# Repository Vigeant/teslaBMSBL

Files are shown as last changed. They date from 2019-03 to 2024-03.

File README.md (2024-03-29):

# teslaBMSBL

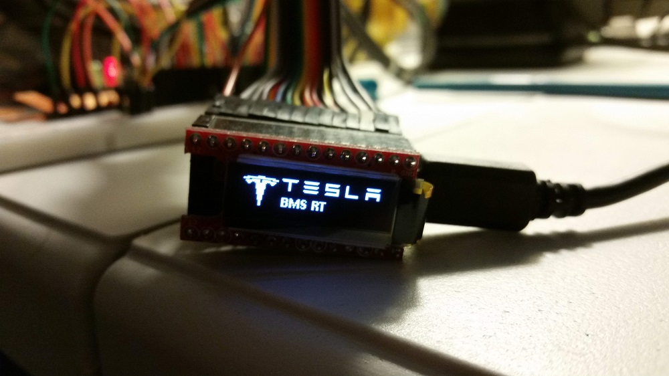
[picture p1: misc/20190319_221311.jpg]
Tesla BMS BL

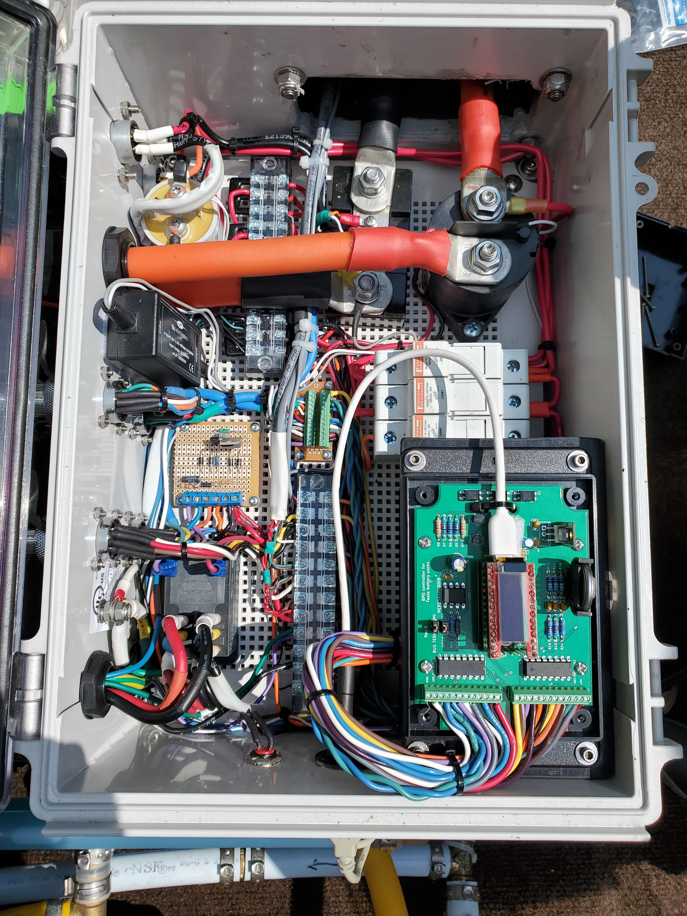
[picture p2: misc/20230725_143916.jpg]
Tesla BMS BL board


## Hardware

see eagle files to build the board hosting the teensy 3.2.

## dependencies

- TeensyView libs
  - <https://github.com/sparkfun/SparkFun_TeensyView_Arduino_Library/tree/master/examples>
- Snooze for lower power consumption
  - <https://github.com/duff2013/Snooze>

## Error codes on teensyView

| code | definition |
|:----:|---|
| A | Modules Fault Loop |
| B | Battery Monitor Fault |
| C | BMS Serial communication Fault |
| D | BMS Cell Over Voltage Fault |
| E | BMS Cell Under Voltage Fault |
| F | BMS Over Temperature Fault |
| G | BMS Under Temperature Fault |
| H | BMS 12V Battery Over Voltage Fault |
| I | BMS 12V Battery Under Voltage Fault |
| J | BMS Water Sensor 1 Fault |
| K | BMS Water Sensor 2 Fault |
| L | Incorrect modules count |

## Connection to USB serial console

Serial Line: COMX (X typically = 7)
Speed: 115200

## controller state machine

<!-- [State machine](https://online.visual-paradigm.com/w/pmcoivfe/diagrams.jsp#diagram:proj=0&id=3) -->

```mermaid
    stateDiagram-v2

    state "INIT

    outL_12V_bat_chrg_buffer = 1;
    outpwm_pump_buffer = 0;
    outL_evcc_on_buffer = 1;
    outH_fault_buffer = 0;" as INIT

    state "STANDBY

    balanceCells();
    outL_evcc_on_buffer = HIGH;
    outH_fault_buffer = chargerInhibit;
    outL_12V_bat_chrg_buffer = !dc2dcON_H;
    outpwm_pump_buffer = 0;" as STANDBY

    state "RUN

    outL_evcc_on_buffer = LOW;
    outH_fault_buffer = powerLimiter;
    outL_12V_bat_chrg_buffer = LOW;
    outpwm_pump_buffer = YES" as RUN

    state "PRE_CHARGE

    balanceCells();
    outL_evcc_on_buffer = LOW;
    outH_fault_buffer = chargerInhibit;
    outL_12V_bat_chrg_buffer = !dc2dcON_H;
    outpwm_pump_buffer = 0;
    msgStatusIns.bBMSStatusFlags = 0;" as PRE_CHARGE

    state "CHARGING

    balanceCells();
    outL_evcc_on_buffer = LOW;
    outH_fault_buffer = chargerInhibit;
    outL_12V_bat_chrg_buffer = LOW;
    outpwm_pump_buffer = YES;
    msgStatusIns.bBMSStatusFlags = 0;" as CHARGING

    state "TOP_BALANCING

    balanceCells();
    msgStatusIns.bBMSStatusFlags |= BMS_STATUS_CELL_BVC_FLAG;
    outL_evcc_on_buffer = LOW;
    outH_fault_buffer = chargerInhibit;
    outL_12V_bat_chrg_buffer = HIGH;
    outpwm_pump_buffer = YES;
    msgStatusIns.bBMSStatusFlags = BMS_STATUS_CELL_BVC_FLAG;" as TOP_BALANCING

    state "POST_CHARGE

    balanceCells();
    outL_evcc_on_buffer = HIGH;
    outH_fault_buffer = HIGH;
    outL_12V_bat_chrg_buffer = HIGH;
    outpwm_pump_buffer = YES;
    msgStatusIns.bBMSStatusFlags = BMS_STATUS_CELL_HVC_FLAG;" as POST_CHARGE

    [*] --> INIT

    INIT --> STANDBY

    STANDBY --> RUN : INH_RUN == HIGH
    STANDBY --> PRE_CHARGE : getHighCellVolt < charger_cycle_v_setpoint && \ngetHighCellVolt < max_charge_v_setpoint && \nticks >= standbyTicks
    STANDBY --> CHARGING : INH_CHARGING == HIGH

    PRE_CHARGE --> STANDBY : INL_EVSE_DISC == LOW
    PRE_CHARGE --> CHARGING :INH_CHARGING == HIGH
    PRE_CHARGE --> STANDBY : ticks > 100

    CHARGING --> POST_CHARGE : ticks >= 5 && \nINL_EVSE_DISC == LOW || \nINH_CHARGING == LOW
    CHARGING --> TOP_BALANCING : getHighCellVolt >= top_balance_v_setpoint

    TOP_BALANCING --> POST_CHARGE : ticks >= 5 && \nINL_EVSE_DISC == LOW || \nINH_CHARGING == LOW

    POST_CHARGE --> STANDBY : ticks >= 50 && \nINH_CHARGING == LOW

    RUN --> STANDBY : INH_RUN == LOW

```

## todo

- [X] none

## particularities

Due to the 5s deepsleep mode in standby, it is hard to connect the serial console. To make it easier, either connect within 10 minutes of a reset or place the bms in run mode and connect.
Due to the deepsleep mode, it is impossible to simply reprogram the teensy following the first sleep. To facilitate reprogramming, the board will not sleep for 10 minutes following a reset.
The teensyview cannot be shut down as it is connected straight to the VDD pins.

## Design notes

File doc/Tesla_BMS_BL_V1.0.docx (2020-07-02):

# Tesla BMS BL V1.0

Tesla Battery Management System Big Loop Version 1.0


# Overview

The Tesla BMS BL was conceived in the scope of a 1981 Sidewinder conversion to electricity. Although the main function of the controller is to monitor and balance the cells in the Tesla model S modules, it also performs the following functions:

- Controls the Electric Vehicle Charger Controller (EVCC) to initiate a charge.
- Monitors up to two battery compartments for flooding (coolant or water) using water sensors.
- Logs various faults obtained from different sources.
- Controls the coolant pump for the cooling of the tesla modules.
- Monitors and manages the 12V battery by controlling a DC2DC converter.

The controller is optimized to draw very little power from the power pack when in standby.

# Installation

The installation of the Tesla BMS BL must be done according to the following pinout with consideration that the controller functions at 3.3V and is 5V tolerant. Its serial port can talk directly with the Tesla BMS Modules without a voltage converter.

The firmware sources are at https://github.com/Vigeant/teslaBMSBL

The pinout configuration is set in the CONFIG.h file in the project.

Typical IO circuitry to convert and protect the controller:

[insert IO diagram here]

# Operation

The Tesla BMS BL implements a finite state machine that controls all outputs in a predictable way.

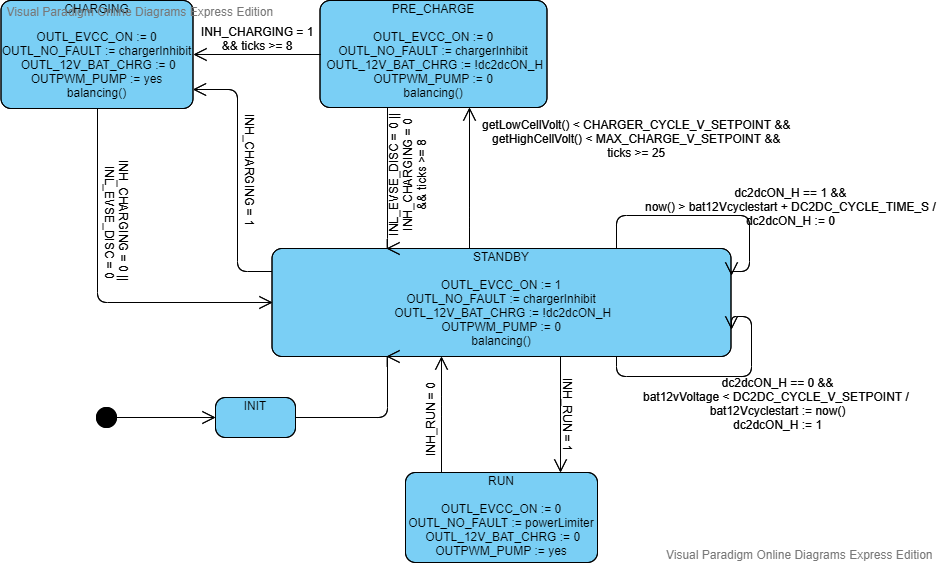
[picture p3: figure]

Figure 1Tesla BMS BL state machine

The state machine is implemented in the controller.cpp file. For simplicity, it is implemented as a mix of a meeley and a moore state machine. The content of the states are the actions and outputs and the transitions typically show the trigger for this transition. When a “/” is present it is used to separate the trigger from the actions on a transition.

The state machine is run at every tick and the default tick rate is 5Hz or every 200ms. The exception is when the controller is in low power mode in the standby state where the controller will sleep for 5 seconds before taking another action.

## OLED display interface

The OLEd display cycles through different formats every 3 seconds to display a quick health check of the modules.

### Tesla BMS BL and eSidewinder splash screens

This is the first format and along with the eSidewinder splash indicates the beginning of the formats cycle.

### Faults

If the controller detects a fault, it will display a format indicating 1 letter fault codes:

Fault Code | Definition
A | Modules Fault Loop
B | Battery Monitor Fault
C | BMS Serial communication Fault
D | BMS Cell Over Voltage Fault
E | BMS Cell Under Voltage Fault
F | BMS Over Temperature Fault
G | BMS Under Temperature Fault
H | BMS 12V Battery Over Voltage Fault
I | BMS 12V Battery Under Voltage Fault
J | BMS Water Sensor 1 Fault
K | BMS Water Sensor 2 Fault

Figure 2 faults table

### sFaults (Sticky Faults)

When a fault is resolved, the fault will disappear from the faults format but all faults that occurred since the last reset will be displayed in the sticky faults format.

### VBat and TBat

VBat Displays the total voltage of the Battery.

TBat display the average Temperature of the battery.

### VClo VChi

VClo displays the voltage of the cell with the lowest voltage.

VChi displays the voltage of the cell with the highest voltage.

### VCmin VCmax

VCmin displays the lowest voltage a cell reached since the last reset.

VCmax displays the highest voltage a cell reached since the last reset.

### VCdiff Tmax

VCdiff displays the delta between the highest cell voltage and the lowest cell voltage. This is a good indicatore of how balanced the battery pack is.

Tmax displays the highest temperature reading of all the sensors.

### State

Displays the name of the state the controller is currently in. Refer to Figure 1 for the state machine.

## Firmware Update

The firmware must be updated using the sources and the Arduino IDE tool chain for the Teensy 3.2.

## Command Line Interface (CLI)

The command line interface offers a more detailed view of the battery packs to help investigate issues. It offers various verbose levels and three main functions.

To connect to the CLI you must:

1. Connect a PC to the Teensy 3.2 via a usb cable.
2. Identify the COMX that was assigned to the USB to Serial adapter. In the screenshot below, it is COM7.

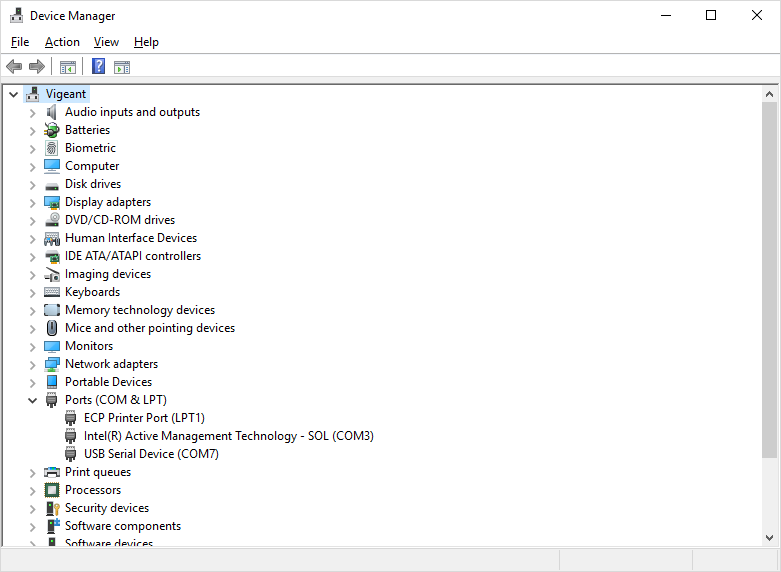
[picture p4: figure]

3. Using a terminal emulator of your choice, connect to the serial port using a baud rate of 115200. For example, if using putty, it would look as follows. The connection will fail when the board in sleeping. To ease the connection, the board is prevented from sleeping for 1 minute following a reset and also does not sleep when in any other state than standby. The controller will not sleep as long as a serial connection is established.

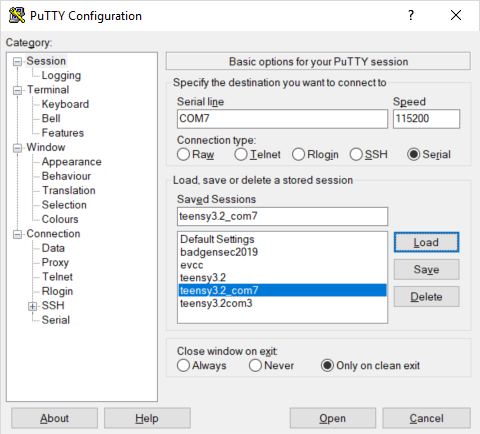
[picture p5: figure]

4. Once connected, you will be presented with a black screen and can press enter to show the prompt. Typing help or “?” will display the help for the CLI.

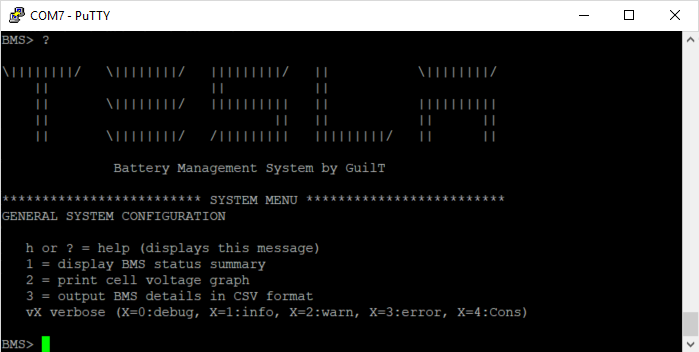
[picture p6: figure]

5. Here is an example of the “1” option when connected to two tesla modules:

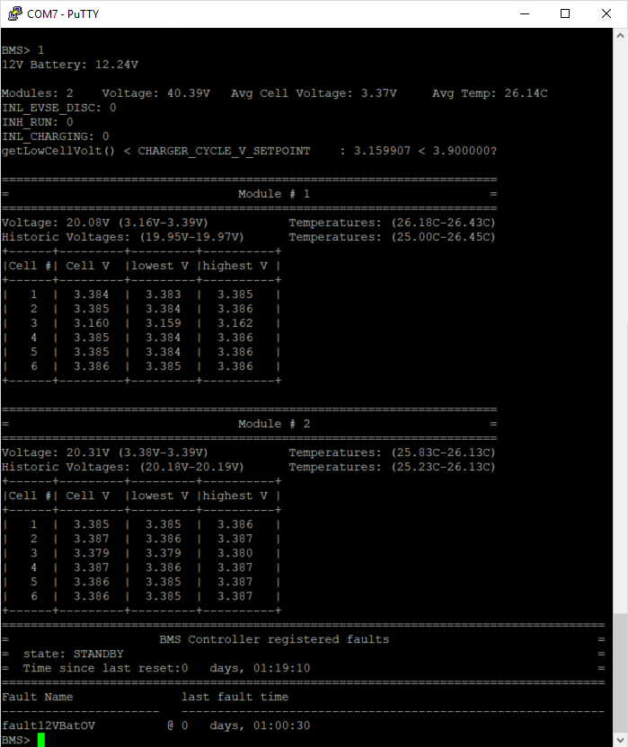
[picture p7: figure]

Notice how it provides all the detailed information about each cell in each module as well as the state of the other inputs and the 12V battery. It also provides the last time a fault occurred.

6. Option 2 provides an ascii art bar graph of the voltage of each cell. This is useful to get a quick glance at the balancing of the cells. Notice that the voltage is automatically scaled to cover the delta between the highest and lowest cell.

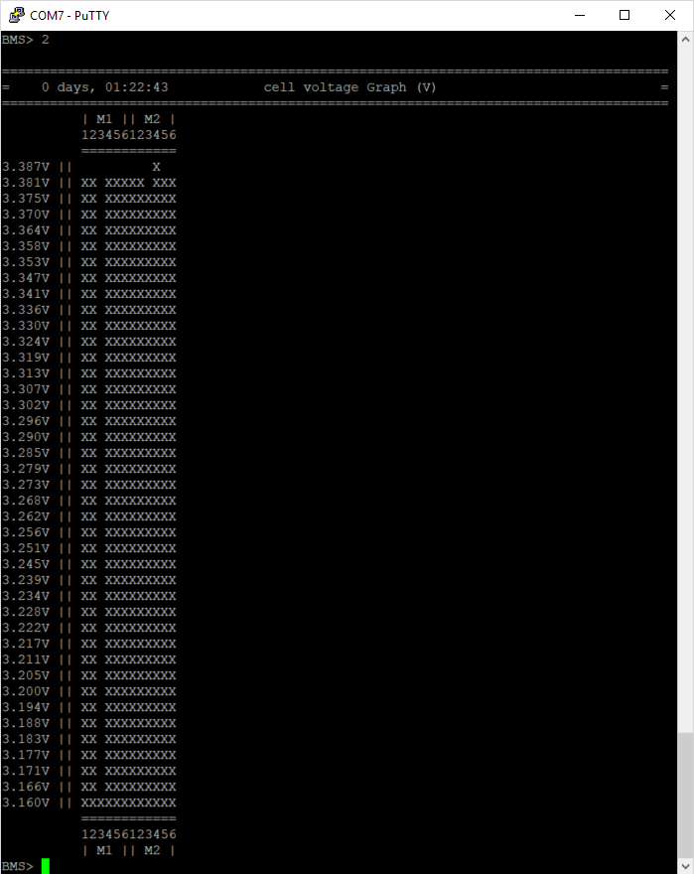
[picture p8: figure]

7. Option 3 displays the states of each cells and the two temperature sensors in CSV format for easy export into excel.
8. When done, close the putty window and the board will go back into normal operation sleeping in the standby state.

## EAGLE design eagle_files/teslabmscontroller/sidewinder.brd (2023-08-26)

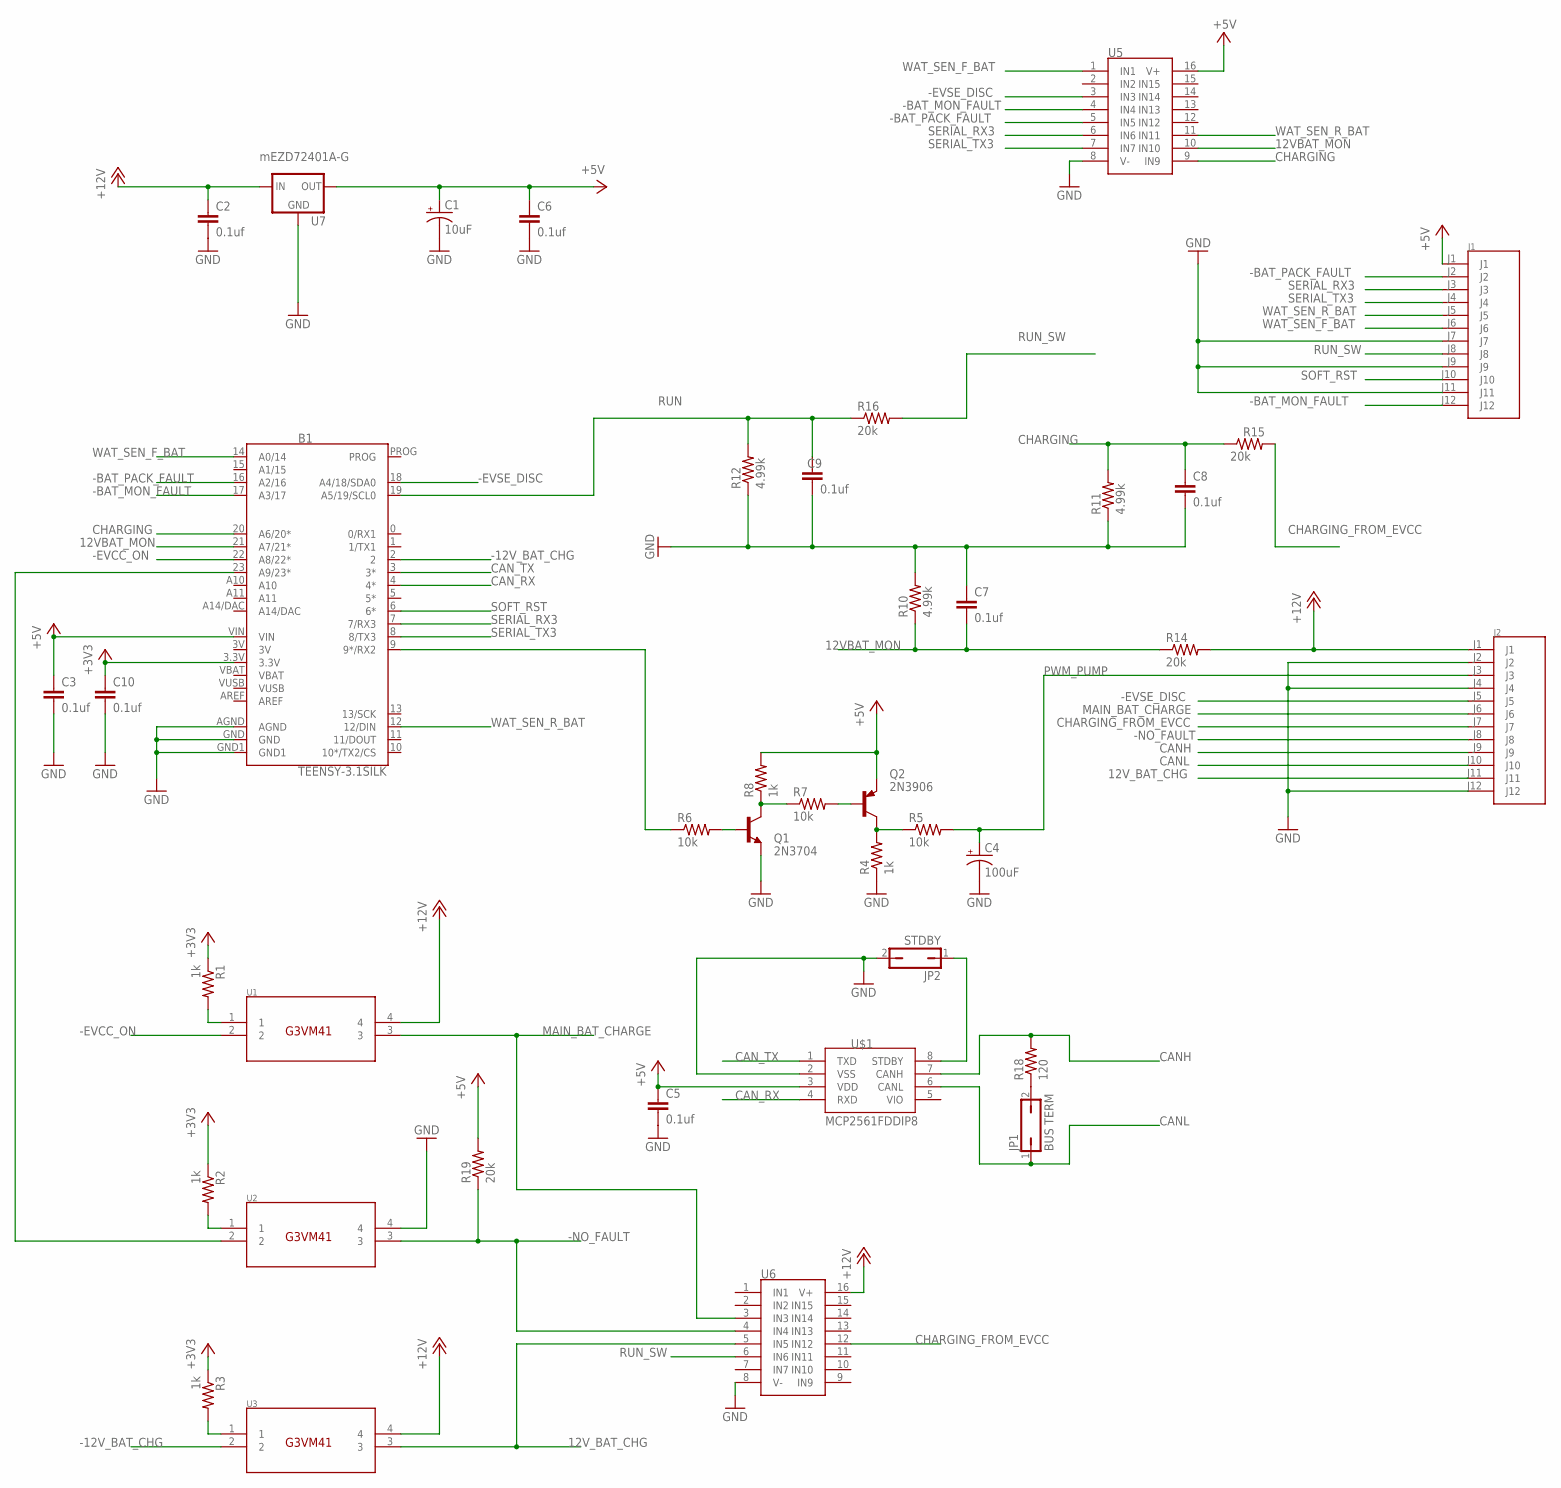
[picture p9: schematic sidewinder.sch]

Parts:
B1: TEENSY-3.1SILK; TEENSY-3.1
C1: 10uF; CPOL-RADIAL-2.5MM-5MM
C2, C3, C5, C6, C7, C8, C9, C10: 0.1uf; C2.5-2
C4: 100uF; CPOL-RADIAL-2.5MM-6.5MM
J1, J2: TERMINAL12
JP1: BUS TERM; JP1
JP2: STDBY; JP1
Q1: 2N3704; TO92
Q2: 2N3906; TO92
R1, R2, R3, R4, R8: 1k; 0207/10
R5, R6, R7: 10k; 0207/10
R10, R11, R12: 4.99k; 0207/10
R14, R15, R16, R19: 20k; 0207/10
R18: 120; 0207/10
U1, U2, U3: G3VM41
U5, U6: SP720APP; DIP16
U7: mEZD72401A-G; TO220-IGO
U$1: MCP2561FDDIP8; DIP787W45P254L949H533Q8B

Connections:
3V: B1.3V
12VBAT_MON: B1.21 (A7/21*), C7.2, R10.1, R14.1, U5.10 (IN10)
12V_BAT_CHG: J2.J11, U3.3, U6.5 (IN5)
+3V3: B1.3.3V, C10.1, R1.1, R2.1, R3.1
+5V: B1.VIN, C1.1 (+), C3.1, C5.1, C6.1, J1.J1, Q2.3 (E), R8.2, R19.2, U5.16 (V+), U7.OUT, U$1.3 (VDD)
+12V: C2.1, J2.J1, R14.2, U1.4, U3.4, U6.16 (V+), U7.IN
-12V_BAT_CHG: B1.2, U3.2
-BAT_MON_FAULT: B1.17 (A3/17), J1.J12, U5.4 (IN4)
-BAT_PACK_FAULT: B1.16 (A2/16), J1.J2, U5.5 (IN5)
-EVCC_ON: B1.22 (A8/22*), U1.2
-EVSE_DISC: B1.18 (A4/18/SDA0), J2.J5, U5.3 (IN3)
-NO_FAULT: J2.J8, R19.1, U2.3, U6.4 (IN4)
CANH: J2.J9, R18.2, U$1.7 (CANH)
CANL: J2.J10, JP1.1, U$1.6 (CANL)
CAN_RX: B1.4 (4*), U$1.4 (RXD)
CAN_TX: B1.3 (3*), U$1.1 (TXD)
CHARGING: B1.20 (A6/20*), C8.1, R11.2, R15.1, U5.9 (IN9)
CHARGING_FROM_EVCC: J2.J7, R15.2, U6.12 (IN12)
GND: B1.AGND, B1.GND, B1.GND1, C1.2 (-), C2.2, C3.2, C4.2 (-), C5.2, C6.2, C7.1, C8.2, C9.2, C10.2, J1.J7, J1.J9, J1.J11, J2.J2, J2.J4, J2.J12, JP2.2, Q1.3 (E), R4.1, R10.2, R11.1, R12.1, U2.4, U5.8 (V-), U6.8 (V-), U7.GND, U$1.2 (VSS)
MAIN_BAT_CHARGE: J2.J6, U1.3, U6.3 (IN3)
unnamed: B1.23 (A9/23*), U2.2
unnamed: B1.9 (9*/RX2), R6.1
unnamed: Q1.1 (B), R6.2
unnamed: Q1.2 (C), R7.1, R8.1
unnamed: Q2.2 (B), R7.2
unnamed: R1.2, U1.1
unnamed: R2.2, U2.1
unnamed: R3.2, U3.1
unnamed: Q2.1 (C), R4.2, R5.1
unnamed: JP2.1, U$1.8 (STDBY)
unnamed: JP1.2, R18.1
PWM_PUMP: C4.1 (+), J2.J3, R5.2
RUN: B1.19 (A5/19/SCL0), C9.1, R12.2, R16.1
RUN_SW: J1.J8, R16.2, U6.6 (IN6)
SERIAL_RX3: B1.7 (7/RX3), J1.J3, U5.6 (IN6)
SERIAL_TX3: B1.8 (8/TX3), J1.J4, U5.7 (IN7)
SOFT_RST: B1.6 (6*), J1.J10
VBAT: B1.VBAT
VUSB: B1.VUSB
WAT_SEN_F_BAT: B1.14 (A0/14), J1.J6, U5.1 (IN1)
WAT_SEN_R_BAT: B1.12 (12/DIN), J1.J5, U5.11 (IN11)

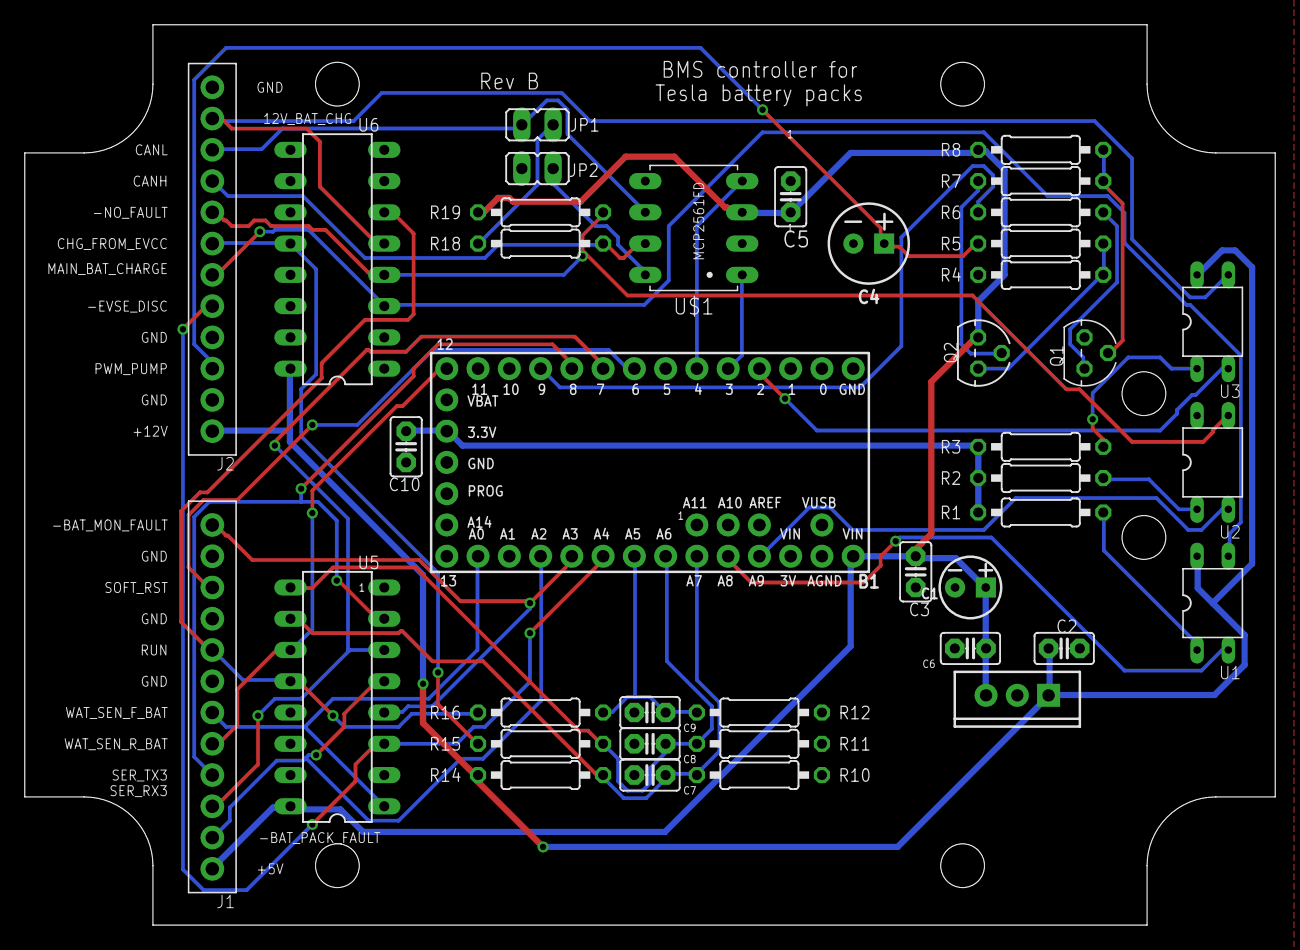
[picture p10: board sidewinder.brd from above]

Board: 2 copper layers, 101.6 x 73.2 mm, 40 parts (0 on the bottom side), 38 nets.

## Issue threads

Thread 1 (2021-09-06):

Connection pinout.

waleedam, 2021-09-06:
hello Thanks for the great work. I have an issue with my battery I'm trying to figure out what causing the faults.
can you help me by telling me the wiring from teensy/ Arduino to BMS board? where should I connect the wiring from teensy to?

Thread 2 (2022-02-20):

New features

marlinarnz, 2022-02-20:
First of all: Massive thanks for that great job here. I soldered your PCB, connected it to some Tesla modules - and it works! Also, I like your code style. Does this BMS run in a boat or is it on the road somewhere?

I have some features in mind, that would be nice:
- CAN-bus communication: Create a new class and include it into the main state machine to communicate with OBC/EVCC, MCU, and VCU
- Battery heating control (for charging in cold months/regions): Add pins for a battery heater and a valve and include a logic into the Controller state machine
- Add a shunt (common feature of a BMS)
- Control the main contactor and precharge relay: Add corresponding pins and states in the Controller state machine
- Calculate the SOC

Are you interested in further work on this project? In this case, I'd really like to contribute to these features. Otherwise, I'd just fork it and work on independently. I want to make this BMS work in conjunction with my [VCU project](https://github.com/marlinarnz/eVCU) in an EV conversion.

Cheers!

Vigeant, 2022-02-20:
Thanks, yes it's in a boat conversion that will hit the water next summer.
Expect some more bug fixes this summer. We converted a 1981 sidewinder
lowpro with an 1974 Johnson 135hp. We replaced the 2stroke block but kept
the boat look as vintage as possible.

Can bus will come. It's on the PCB.
We have a dedicated charger controller that I power cycle to start a
charge.
SoC from shunt is managed by another system.

I ran out of pins on this controller. I would need a gpio extender to do
more.

It's probably best to fork it for your purpose. I can also send you our
architecture diagrams if you'd like.

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

marlinarnz, 2022-02-20:
Thanks for the quick reply. Sound like a cool project. I'll fork it then and look out for your CAN implementation. I might be implementing it next month, too. And having a look at your diagrams would be nice!

Vigeant, 2022-08-05:
Hi @marlinarnz, How is your conversion project going? I looked at your fork and will merge in a lot of the tweaks and cleanups you made including an extra balancing state. Our boat finally hit the water this summer and we debugged many things. Were going to do a car as well soon so interested to see where your fork is going. I also made a version 2 of the PCB mostly to change the voltage regulator to a switching one as the heat was a problem.

Vigeant, 2022-08-05:
https://youtu.be/jw3WkO8erGM

marlinarnz, 2022-08-08:
Hi @Vigeant, thanks for the update. It's great to hear that your eSidewinder works! It looks quite powerful in the video. Congrats!

The car conversion progresses slowly. I have all crucial parts at home, the software architecture works, and I finally finished rust proofing of the chassey. I was about to put it all together, but then my RasPie suddenly denied his CAN bus services, the ESP32 refused new flashing, and I got distracted by summer. I'll pick it up in September.

I'm glad you approve my changes. The last time, I looked into the BMS, I was about to re-design the PCB in order to make it more suitable for a car conversion (see PCB features TODO in Readme of [my fork](https://github.com/marlinarnz/teslaBMSBL)).
[This is how far I came](https://github.com/Vigeant/teslaBMSBL/files/9285032/Schematic_TeslaBMS_RevC_2022-08-08.pdf) (still needs the cooling/heating circuitry). Tell me what you think. I can also share the project on easyEDA.

Vigeant, 2022-08-09:
@marlinarnz PM me and I will send you our schematics. Also I cannot see your CAN class in your repo. I would like to have a look and possibly merge it ; )

marlinarnz, 2022-08-10:
Hi, PMs are not supported by GitHub. I hope this works.
I just pushed the CAN class, which I forgot last time.

The circuitry I showed you is based on your eagle files from RevA, but I saw that you pushed a new version a few days ago. If you want to start off with a car conversion, it makes sense to design a PCB together. I think the ToDos in my fork’s readme are appropriate, but I don’t have much experience in PCB layout, to be honest.

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

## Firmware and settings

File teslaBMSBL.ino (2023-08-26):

/**@file teslaBMSBL.ino */
#include <Arduino.h>
#include "Controller.hpp"
#include "Cons.hpp"
#include "Logger.hpp"
#include "Oled.hpp"
#include <Snooze.h>
#include <TimeLib.h>

#include <TeensyView.h>

/*! \mainpage teslaBMSBL

   \section intro_sec Introduction

   A teensy based battery management system for Tesla battery modules.

   \section install_sec Installation

   \subsection step1 Step 1: Opening the box

   etc...
*/

//instantiate all objects
TeensyView teensyView_inst(OLED_PIN_RESET, OLED_PIN_DC, OLED_PIN_CS, OLED_PIN_SCK, OLED_PIN_MOSI);
//static Settings settings;
static Controller controller_inst;        ///< The controller is responsible for orchestrating all major functions of the BMS.
static Cons cons_inst(&controller_inst);  ///< The console is a 2 way user interface available on usb serial port at baud 115200.
static Oled oled_inst(&controller_inst, &teensyView_inst);  ///< The oled is a 1 way user interface displaying the most critical information.

// Load drivers
//SnoozeTouch touch;
SnoozeDigital digital;
SnoozeTimer timer;
SnoozeUSBSerial usbSerial;

// install drivers to a SnoozeBlock
SnoozeBlock config(timer, digital, usbSerial);

time_t getTeensy3Time() {
  return Teensy3Clock.get();
}
/////////////////////////////////////////////////
/// \brief The setup function runs once when you press reset or power the board.
/////////////////////////////////////////////////
void setup() {

  Serial.println("setup");
  pinMode(INL_SOFT_RST, INPUT_PULLUP);
  Serial.println("setup pinmode");
  // set the Time library to use Teensy 3.0's RTC to keep time
  setSyncProvider(getTeensy3Time);
  Serial.println("setup setSyncProvider");
  delay(100);
  if (timeStatus() != timeSet) {
    Serial.println("Unable to sync with the RTC");
  } else {
    Serial.println("RTC has set the system time");
  }
  Serial.println("setup");
  LOG_CONSOLE("BMS> ");
}


/////////////////////////////////////////////////
/// Holds all the code that runs every period.
/////////////////////////////////////////////////
void phase1main() {
  if (digitalRead(INL_SOFT_RST) == LOW) {
    //_reboot_Teensyduino_();
    CPU_RESTART;
  }
  cons_inst.doConsole();
}

/////////////////////////////////////////////////
/// Holds code that runs every two periods.
/////////////////////////////////////////////////
void phase1A() {
  controller_inst.doController();
}

/////////////////////////////////////////////////
/// Holds code that runs every two periods.
/////////////////////////////////////////////////
void phase1B() {
  oled_inst.doOled();
}

/////////////////////////////////////////////////
/// Once setup is complete, loop is called for ever.
/////////////////////////////////////////////////
void loop() {
  uint32_t starttime, endtime, delaytime, timespent, period;
  bool phaseA = true;

  for (;;) {
    starttime = millis();

    phase1main();
    if (phaseA)
      phase1A();
    else
      phase1B();
    phaseA = !phaseA;

    digital.pinMode(INL_SOFT_RST, INPUT_PULLUP, FALLING);  //pin, mode, type

    //get loop period from controller
    period = controller_inst.getPeriodMillis();

    endtime = millis();
    if (endtime > starttime) {
      timespent = endtime - starttime;
    } else {
      starttime = 0xffffffff - starttime;
      timespent = starttime + endtime;
    }
    if (timespent >= period) {
      delaytime = 0;
    } else {
      delaytime = period - timespent;
    }

    //sleep board instead of delay, if not in active state
    if (delaytime > LOOP_PERIOD_ACTIVE_MS) {
      timer.setTimer(delaytime);  // milliseconds
      //who = Snooze.deepSleep( config );
      (void)Snooze.deepSleep(config);
    } else {
      delay(delaytime);
    }
  }
}

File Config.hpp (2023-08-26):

#pragma once

#include <Arduino.h>
#include <EEPROM.h>
#include <list>

//enable testing mode that simply cycles through all states instead of triggers
//#define STATECYCLING 1
#define TESTING_MODE 0

///////////////////////////////////
// Teensy pin configuration      //
///////////////////////////////////
//side 1
//#define SERIAL1_RX          0
//#define SERIAL1_TX          1
#define OUTL_12V_BAT_CHRG 2  //Drive low to turn the DC2DC converter to charge the 12V battery
#define CAN_TX 3
#define CAN_RX 4
#define OLED_PIN_DC 5
#define INL_SOFT_RST 6  // soft reset of the teensy
#define SERIAL3_RX 7    // from Tesla BMS
#define SERIAL3_TX 8    // to Tesla BMS
#define OUTPWM_PUMP 9   // PWM to coolant pump
#define OLED_PIN_CS 10
#define OLED_PIN_MOSI 11
#define INL_WATER_SENS1 12  // battery enclosure water sensor 1

//side 2
#define OLED_PIN_SCK 13     //LED
#define INL_WATER_SENS2 14  // battery enclosure water sensor 2
#define OLED_PIN_RESET 15
#define INL_BAT_PACK_FAULT 16  //Tesla Battery pack fault.
#define INL_BAT_MON_FAULT 17   //Battery Monitor Fault.
#define INL_EVSE_DISC 18       //Electric Vehicle Supply Equipment Disconnected (from EVCC). (set Out2)
#define INH_RUN 19             //RUN signal from power relay with voltage divider from 12V to 3.3V.
#define INH_CHARGING 20        //CHARGING signal from EVCC. (Set Out1 to charging switched 12V)
#define INA_12V_BAT A7         //PIN21 12v battery monitor. Analog input with 12V to 3.3V voltage divider.
#define OUTL_EVCC_ON 22        //drive low to power on EVCC. Cycling this signal will force a new charge cycle.
#define OUTH_FAULT 23          //drive low to signal no fault to EVCC. Required for EVCC to charge.

//top side
//short P and G to reset board into program mode using push button

//Set to the proper port for your USB connection - SerialUSB on Due (Native) or Serial for Due (Programming) or Teensy
#define SERIALCONSOLE Serial

/*
   State machine
*/
// Loop periods for the state machine of the controller
#define LOOP_PERIOD_ACTIVE_MS 200
#define LOOP_PERIOD_STANDBY_MS 2000

#define EEPROM_VERSION 6

#define CPU_RESTART_ADDR (uint32_t *)0xE000ED0C
#define CPU_RESTART_VAL 0x5FA0004
#define CPU_RESTART (*CPU_RESTART_ADDR = CPU_RESTART_VAL);

class Param {
public:
  Param(const char* paramName, bool editable, const char* description)
    : paramName(paramName),
      editable(editable),
      description(description) {
    ;
  }
  const char* paramName;
  virtual void prettyPrint();
  virtual int32_t setVal(const char* valStr);
  virtual uint16_t getSize();
  virtual void resetDefault();
  virtual uint32_t saveToEEPROM(uint32_t address);
  virtual uint32_t loadFromEEPROM(uint32_t address);
protected:
  bool editable = true;
  const char* description;
};

template<class C> class ParamImpl : public Param {
public:
  ParamImpl(const char* paramName, bool editable, C value, C valueDefault, C valueMin, C valueMax, const char* description)
    : Param(paramName, editable, description),
      value(value),
      valueDefault(valueDefault),
      valueMin(valueMin),
      valueMax(valueMax) {
    ;
  }

  void prettyPrint();
  int32_t setVal(const char*);

  C getVal() {
    return value;
  }

  void resetDefault() {
    value = valueDefault;
  }

  uint16_t getSize();
  bool valueMatchDefault() {
    return (value == valueDefault);
  }

  uint32_t saveToEEPROM(uint32_t address) {
    EEPROM.put(address, value);
    return sizeof(C);
  }

  uint32_t loadFromEEPROM(uint32_t address) {
    EEPROM.get(address, value);
    return sizeof(C);
  }

private:
  C value;
  C valueDefault;
  C valueMin;
  C valueMax;
};
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

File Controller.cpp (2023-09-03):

#include "FlexCAN.h"
#include "Controller.hpp"

/////////////////////////////////////////////////
/// \brief When instantiated, the controller is in the init state ensuring that all the signal pins are set properly.
/////////////////////////////////////////////////
Controller::Controller()
  : faultModuleLoop(String("ModuleLoop"), String("A"), true, true, String("One or more BMS modules have asserted the fault loop!\n"), String("All modules have deasserted the fault loop\n")),
    faultBatMon(String("BatMon"), String("B"), false, true, String("The battery monitor asserted a fault!\n"), String("The battery monitor deasserted a fault\n")),
    faultBMSSerialComms(String("BMSSerialComms"), String("C"), true, true, String("Serial communication with battery modules lost!\n"), String("Serial communication with battery modules re-established!\n")),
    faultBMSOV(String("BMSOV"), String("D"), true, true, String("A cell reached a voltage higher than the OV threshold\n"), String("All cells are back under OV threshold\n")),
    faultBMSUV(String("BMSUV"), String("E"), false, true, String("A cell reached a voltage lower than the UV threshold\n"), String("All cells are back over UV threshold\n")),
    faultBMSOT(String("BMSOT"), String("F"), true, true, String("A module reached a temp higher than the OT threshold\n"), String("All modules are back under OT threshold\n")),
    faultBMSUT(String("BMSUT"), String("G"), true, true, String("A module reached a temp lower than the UT threshold\n"), String("All modules are back over UT threshold\n")),
    fault12VBatOV(String("12VBatOV"), String("H"), false, false, String("12V battery reached a voltage higher than the OV threshold\n"), String("12V battery back under the OV threshold\n")),
    fault12VBatUV(String("12VBatUV"), String("I"), false, true, String("12V battery reached a voltage lower than the UV threshold\n"), String("12V battery back over the UV threshold\n")),
    faultWatSen1(String("WatSen1"), String("J"), true, true, String("The battery water sensor 1 is reporting water!\n"), String("The battery water sensor 1 is reporting dry.\n")),
    faultWatSen2(String("WatSen2"), String("K"), true, true, String("The battery water sensor 2 is reporting water!\n"), String("The battery water sensor 2 is reporting dry.\n")),
    faultIncorectModuleCount(String("IncorectModuleCount"), String("L"), true, true, String("Found a different ammount of modules than configured!\n"), String("Found all modules as configured!\n")),
    bms(&settings) {
  state = INIT;

  msg.ext = 1;
  msg.id = BMS_EVCC_STATUS_IND;
  msg.len = 5;
  msg.buf[0] = 0;
  msg.buf[1] = 0;
  msg.buf[2] = 0;
  msg.buf[3] = 0;
  msg.buf[4] = 0;

  msgStatusIns.bBMSStatusFlags = 0;
  msgStatusIns.bBmsId = 0;
  msgStatusIns.bBMSFault = 0;
  msgStatusIns.bReserved2 = 0;
  msgStatusIns.bReserved3 = 0;

  //try to load object
  settings.loadAllSettingsFromEEPROM(0);
  if (!((settings.magic_bytes.valueMatchDefault()) && (settings.eeprom_version.valueMatchDefault()))) {
    Serial.print("EEPROM does not match magicbytes and version\n");
    (void)reloadDefaultSettings();
    Serial.print("Default values reloaded\n");
  } else {
    Serial.printf("Loaded config from EEPROM|| magicbytes: 0x%X, version = %d\n", settings.magic_bytes.getVal(), settings.eeprom_version.getVal());
  }

  faults.push_back(&faultModuleLoop);
  faults.push_back(&faultBatMon);
  faults.push_back(&faultBMSSerialComms);
  faults.push_back(&faultBMSOV);
  faults.push_back(&faultBMSUV);
  faults.push_back(&faultBMSOT);
  faults.push_back(&faultBMSUT);
  faults.push_back(&fault12VBatOV);
  faults.push_back(&fault12VBatUV);
  faults.push_back(&faultWatSen1);
  faults.push_back(&faultWatSen2);
  faults.push_back(&faultIncorectModuleCount);
  //Serial.print("Controller faults created\n");
}


int32_t Controller::saveSettings() {
  settings.saveAllSettingsToEEPROM(0);
  return 0;
}

int32_t Controller::reloadDefaultSettings() {
  settings.reloadDefaultSettings();
  return saveSettings();
}

/////////////////////////////////////////////////
/// \brief Orchestrates the activities within the BMS via a state machine.
/////////////////////////////////////////////////
void Controller::doController() {
  //Serial.print("doController\n");
  static int ticks = 0;
  static unsigned int bat12Vcyclestart = 0;
  static int standbyTicks = 1;  //1 because ticks slow down
  const int stateticks = 4;

  msgStatusIns.bBMSStatusFlags = 0;
  msgStatusIns.bBMSFault = 0;

  if (canOn == false && settings.canbus_to_EVCC.getVal() == 1) {
    Can0.begin(settings.canbus_speed.getVal());
    canOn = true;
  }

  if (canOn == true && settings.canbus_to_EVCC.getVal() == 0) {
    Can0.end();
    canOn = false;
  }

  //Serial.print("doController can done\n");

  bat12vVoltage = (float)analogRead(INA_12V_BAT) / settings.bat12v_scaling_divisor.getVal();

  if (state != INIT) syncModuleDataObjects();

  //Serial.print("doController syncModuleDataObjects\n");

  //figure out state transition
  switch (state) {
    /**************** ****************/
    case INIT:
      if (ticks >= stateticks) {
        ticks = 0;
        state = STANDBY;
        lastResetTimeStamp = now();
        LOG_INFO("Transition to STANDBY\n");
      }
      break;
    /**************** ****************/
    case STANDBY:
#ifdef STATECYCLING
      if (ticks >= stateticks) {
        ticks = 0;
        state = PRE_CHARGE;
        LOG_INFO("Transition to PRE_CHARGE\n");
      }
#else
      if (dc2dcON_H == 0 && bat12vVoltage < settings.dc2dc_cycle_v_setpoint.getVal()) {
        bat12Vcyclestart = (millis() / 1000);
        dc2dcON_H = 1;
      } else if (dc2dcON_H == 1 && ((millis() / 1000) > bat12Vcyclestart + settings.dc2dc_cycle_time_s.getVal())) {
        // I am ignoring the time counter loop around as it will simply result in a short charge cycle
        // followed with a proper charging cycle.
        dc2dcON_H = 0;
      }

      if (digitalRead(INH_RUN) == HIGH) {
        ticks = 0;
        state = RUN;
        LOG_INFO("Transition to RUN\n");
      } else if (digitalRead(INH_CHARGING) == HIGH) {
        ticks = 0;
        state = CHARGING;
        LOG_INFO("Transition to CHARGING\n");
      } else if (bms.getHighCellVolt() < settings.charger_cycle_v_setpoint.getVal() && bms.getHighCellVolt() < settings.max_charge_v_setpoint.getVal() && ticks >= standbyTicks) {
        ticks = 0;
        state = PRE_CHARGE;
        LOG_INFO("Transition to PRE_CHARGE\n");
      }
#endif
      break;
    /**************** ****************/
    case PRE_CHARGE:
#ifdef STATECYCLING
      if (ticks >= stateticks) {
        ticks = 0;
        state = CHARGING;
        LOG_INFO("Transition to CHARGING\n");
      }
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

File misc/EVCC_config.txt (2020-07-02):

Indication Default Function
LED OUT1 tracks the state of the EVCC LED3
CHARGE ON when charging
BUZZER OUT3 ON when the Pack is in HVC or LVC or the cell loop is not good
J1772_DISCONNECTED OUT2 ON when the J1772 cable is disconnected4
HVC ON when the Pack is in HVC (only available when using a CAN BMS)
LVC ON when the Pack is in LVC (only available when using a CAN BMS)


evcc> reset profile 1
evcc> set profile 1
evcc> set linec J1772
evcc> set maxv 168.0
evcc> set out1 CHARGE
evcc> set out3 CHARGE
evcc> set termt 24.0
evcc> enable loopground

evcc> show config
  bms      : loop
  canbr    : 250kbps
  OUT1     : CHARGE
  OUT2     : EVSEDISC
  OUT3     : CHARGE
  charger  : tsm2500
  linec    :  J1772
  maxv     : 168.0V
  maxc     :   2.0A
  termc    :   0.1A
  termt    :  24.0hr
  options  : canterm (CAN termination resistor enabled)
           : loopground (loop OK if loop2 grounded)

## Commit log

2019-03-22 added print summaries to the console
2019-03-22 added colant pump pwm
2019-03-25 worked on state machine
    [BMS_models.xlsx]
2019-03-27 completed battery summary
2019-03-27 added 12V bat stats
2019-03-27 fixed bug in controller
    [Controller.cpp]
2019-04-28 added hysterisy for faults
    after witnessing some fault glitches, we added hysteresy that requires the fault to be present for three ticks for it to be considered.
    Fixed coolant pump scaling issue,
    Added some more balancing functionality. More thaught required.
    [BMSModule.cpp, CONFIG.h, Controller.cpp]
2019-05-04 safer behavior
    This will keep the dc2dc on while it waits for the charger to turn on.
2019-05-05 fixed console sometimes dropping a character
    [BMS_models.xlsx]
2019-05-06 added controller fault printout
2019-05-17 showing current vdmax on oled
    [BMS_models.xlsx]
2019-05-26 implemented the two water sensor lines
2019-05-26 fixed init of water sensor pins
    [Controller.cpp]
2019-07-06 adjusted 12v divisor
    [BMS_models.xlsx]
2019-07-11 Update Controller.cpp
    prevents to sleep for 1 minute in standby to allow for reprogramming following a reset.
    [Controller.cpp]
2019-10-27 fixed sleeping
    sleep was preventing balancing
    [Controller.cpp]
2019-10-29 Update Controller.cpp
    flipped the polarity of the PWM controlling the pump
    [Controller.cpp]
2019-11-09 Revert "Update Controller.cpp"
    This reverts commit 1ec6cf16614d8a641a1f77b5105418e0ae55e478.
    [Controller.cpp]
2019-12-27 added PWM test program
2020-03-27 added eagle files
    [sidewinder.brd, sidewinder.sch]
2020-06-14 fixed RUN
    RUN signal was absent from connector
    flipped whole board so silk alligns with OLED
    fixed routing issu of can chip
    [sidewinder.brd, sidewinder.sch]
2020-06-16 bug fixes
    [sidewinder.brd]
2020-06-16 run and charging to zener
    [sidewinder.brd, sidewinder.sch]
2020-06-16 adjusted 12Vto5V deviders
    changed 2 resistors from 10k to 15k after we fried a board...
    [sidewinder.brd, sidewinder.sch]
2020-07-02 added EVCC_config.txt
    added the config of the EVCC controller
    [EVCC_config.txt, sidewinder.brd, sidewinder.sch]
2020-07-02 added standby to charging transition in controller.cpp
    updated the documentation with the new state machine.
    INL_CHARGING changed to INH_CHARGING in the diagram.
2021-08-24 Update Controller.cpp
    added logic to the charging state to stop the charger when the max charge v setpoint is reached.
    Also added a timeout of 100 ticks to the pre-charge state where if the charger did not start it will go back to standby.
2021-08-31 Update Controller.cpp
    added some comments in the state machine to capture some important decisions regarding allowing the EVCC to stay on and allowing to charge when in run mode.
2021-09-06 tweaks
    adjusted 12V scaling
    limit VBat to 1 digit on the OLED
2021-09-06 state machine tweaks
    adjusted the charcher V setpoint to 4.0V from 3.9V but now check the highest cell instead of the lowest cell. This prevents endless cycling of the charger and when the highest cell is below a voltage, its worth charging.
    [CONFIG.h, Controller.cpp]
2022-03-22 Update Controller.cpp
    adjusted pre-charge delay form 3 seconds to 10 seconds.
2022-06-18 Update CONFIG.h
    adjusted fine balancing to 0.02v
2022-06-18 UI modifications
    printing outputs in console formats to help debugging.
2022-07-29 config tweaks
    adjusted some threshold t help balance tighter.
    [CONFIG.h]
2022-07-31 updated BMS board
    fixed can bus chip and changed 5v regulator to a switching to avoid heat.
    [sidewinder.brd, sidewinder.sch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]
2022-08-06 added trickle charge state
    the final charging requires the dc2dc to be turned off to be able to properly measure the the current drop. the trickle charging state is the same as the charging state but turns off the dc2dc and is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
2022-08-08 reworked fault logic
    refactored faults as a struct array and removed a lot of duplicated code.
    [Controller.cpp]
2022-08-25 Implemented real CLI
    Preparing the CLI to accomodate live configuration of the board through CLI.
2022-09-10 param rework
    Building the scafolding for the eeprom config and CLI configuration of all settings.
    [CONFIG.h, Config.cpp, Config.hpp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]
2022-09-11 major configuration rework
    config is now captured in the Settings class.
    - automatically works with the console
    - TODO console set param feature (use of specialized members)
    - TODO serialization of settings in EEPROM and logic to load smartly.
    [Config.cpp, Config.hpp, Controller.cpp]
2022-09-17 config parameters rework
    Added functionality to set config parameters which saves them to the eeprom automatically. When the BMS loads, it loads the config from the EEPROM automatically and verifies the magic bytes and the version are matching. If not matching, it reloads default values. When setting a new param, it checks it within range.
    [Config.cpp, Config.hpp, Cons.cpp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]
2022-10-05 added module count error
    [Config.cpp, Config.hpp, Controller.cpp]
2022-10-07 fixed oled cycling
    fixed oled that would cycle slowly when in deepsleep mode.
    - added a config setting for adjusting how fast the oled cycles.
    [Config.cpp, Config.hpp, Cons.cpp]
2022-10-16 fixed typos in config description
    [Config.cpp, Controller.cpp]
2022-12-03 Update Controller.cpp
    removed the battery monitor fault from the charge fault to allow charging when the battery is very low and bat mon is faulted.
2022-12-05 added CAN bus functionality
    Added CAN bus to EVCC functionality.
    This allows telling the EVCC to scale down current for top balancing mode.
    This also allows telling the EVCC more precise errors such as over voltage, under voltage and over temp.
    [Config.cpp, Config.hpp, Cons.cpp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]
2023-08-26 fixed CAN
    Fixed can bus
    fixed bug on PCB where run input was connected to both 5v and 12v chips.
    [sidewinder.brd, sidewinder.sch]
2023-08-26 timestamps rework and can fix
    Afficher l’heure du last reset plutôt que le temps depuis, maintenant qu’on a un RTC 😉
    Afficher un format simplifié (moins techno) de date and time genre « Aug 8, 2023 16:41:00 »
    Afficher le pack voltage (total) le plus bas (min) et le plus haut (max) détecté, ainsi que les températures minimales et maximale détectées, avec la commande « 1 », idéalement avec le time stamp 😉
    Changer le terme « trickle charge » pour « top balancing » ou « fine balancing » pour le distinguer du « rough balancing »
    [Config.cpp, Config.hpp, Controller.cpp]
2023-08-26 Update Controller.cpp
    fixed a possible charging initiation problem where EVCC might take a while to report its charging.
    [Controller.cpp]
2023-09-01 cooling pump duty enabled
    Re-enabled the cooling pump duty calculation.
2023-09-03 printing fixes

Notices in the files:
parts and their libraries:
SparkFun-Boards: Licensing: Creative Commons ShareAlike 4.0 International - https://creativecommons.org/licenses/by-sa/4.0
